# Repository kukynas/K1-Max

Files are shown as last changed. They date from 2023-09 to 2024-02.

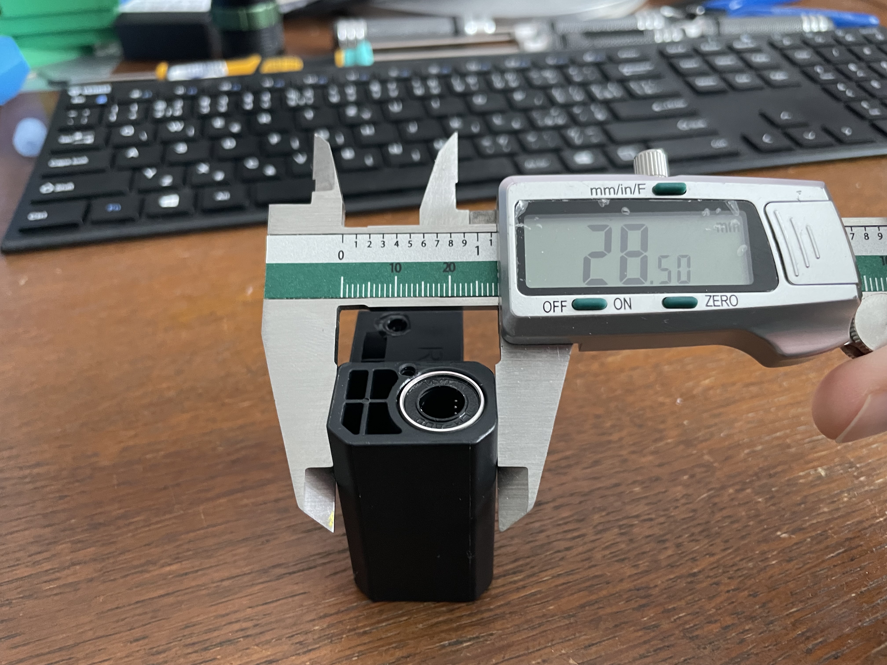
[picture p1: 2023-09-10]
Photo/IMG_5438.JPG

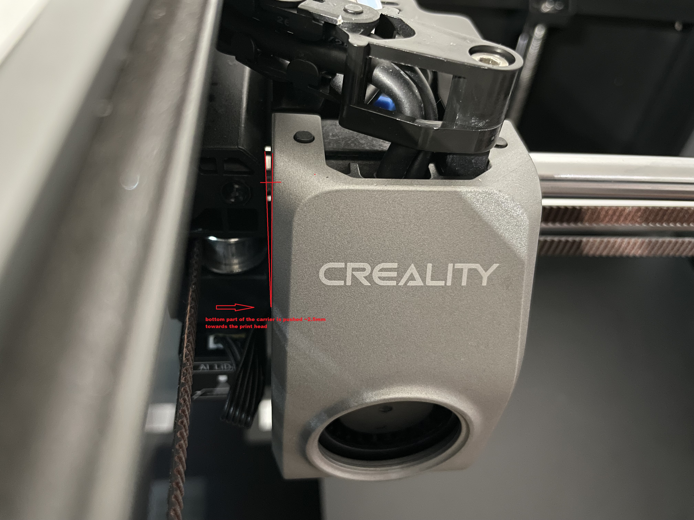
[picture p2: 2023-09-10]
Photo/IMG_5382s.jpg

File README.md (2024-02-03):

# K1 Max
Everything related to Creality K1 Max printer

Work in progress...

Attribution-NonCommercial-ShareAlike 4.0 International (CC BY-NC-SA 4.0)

## Acknowledgements

 - [D3vil Design](https://github.com/D3vil-Design)
 - [Henlor](https://www.printables.com/search/models?q=henlor&ctx=models)
 - And many others

### More info related to K1/Max mods...

Discord: https://discord.gg/QVAN5VNf

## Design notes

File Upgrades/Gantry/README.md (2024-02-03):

# About this mod
It mainly fixes dimensional accuracy, belt path and improve input shaper resonances for both XY axis, the XY rods have much better support by adding mass to the stepper/idler mounts and XY joints, this is full update with new XY joints, new stepper mounts and new idler mounts. One important fact, you'll lose about 5mm of your X travel but build area is bigger than the allowed print area so all should remain the same from print size perspective, you might need to update your printer.cfg if needed and shorten the X travel by few mm, make sure you watch your gantry for the first time as I couldn't test it on K1 (only K1 Max). Gantry is compatible with 16T-26T stepper pulleys so for stepper motors you either use your existing and just change the pulleys to 16T-26T or you'll need new steppers and new pulleys, maximum size of the pulleys allowed is 26T, you will also need to change your printer.cfg parameters, "rotation_distance:" for both X and Y steppers according to your chosen pulley (i.e. 20T x 2mm = 40), sensorless homing "driver_SGTHRS:" for both X and Y, you need to experiment as there's no rule for the correct number, start with 100, if the toolhead doesn't move then go down in 5 increments (95, 90, etc.) if the toolhead is smashing against the frame you need to increase the number (105,110, etc), you might need to cut few teeth from your original belts, how much depends on pulleys chosen, make sure you won't cut too much so that your tensioners are released as much as possible to keep suficient amount of belt/pulley teeth contact for sufficient grip 

# Print setting, orientation etc.
Print with ASA, ABS, PA6/12, PET or any other high temp material, 35-40% infill, 0.16mm layer hight, 4 walls, 8 top/bottom layers, with support as per sliced sample below 




Tolerances are really tigth to prevent potential wobble over time but trimming is not necessary, push/pull the rods in/out couple of times   

# BOM
XY joints:

- 8 x F623ZZ (3x10x4mm) flanged bearings
- 4 x M3x20mm grub screw
- 4 x 0.1-0.2mm M3 washer (between bearings = bearing->washer->bearing)
- 2 x original LM8LUU bearings
- 2 x original M3 screws holding bearings in place

.

Stepper Mounts:

- 12 x F624-2RS or ZZ (4x13x5mm) flanged bearings
- 6 x 0.1-0.2mm M4 washer (between bearings = bearing->washer->bearing)
- 8 x 3x5x5 heat insert
- 8 x M3x6 FHCS screw
- 4 x 0.5mm M3 washer (under the tensioner release screws)
- all the other original parts (tensioners, tensioner idler pin, tensioning screws, stepper screws, original washer used between idlers)

.

Idler Mounts:

- 4 x F624-2RS or ZZ (4x13x5mm) flanged bearings
- 2 x M4x20mm grub screw
- 2 x 0.1-0.2mm M4 washer (between bearings = bearing->washer->bearing)
- 8 x 3x5x5 heat insert
- 8 x M3x6 FHCS screw






.

### More info related to K1/Max mods...

https://discord.gg/QVAN5VNf

Attribution-NonCommercial-ShareAlike 4.0 International (CC BY-NC-SA 4.0)

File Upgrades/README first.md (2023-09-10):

# Print setting for XY joints
Print with ASA, PA6/12, PET or any other higher temp material

Layer height 0.12mm

30% infill

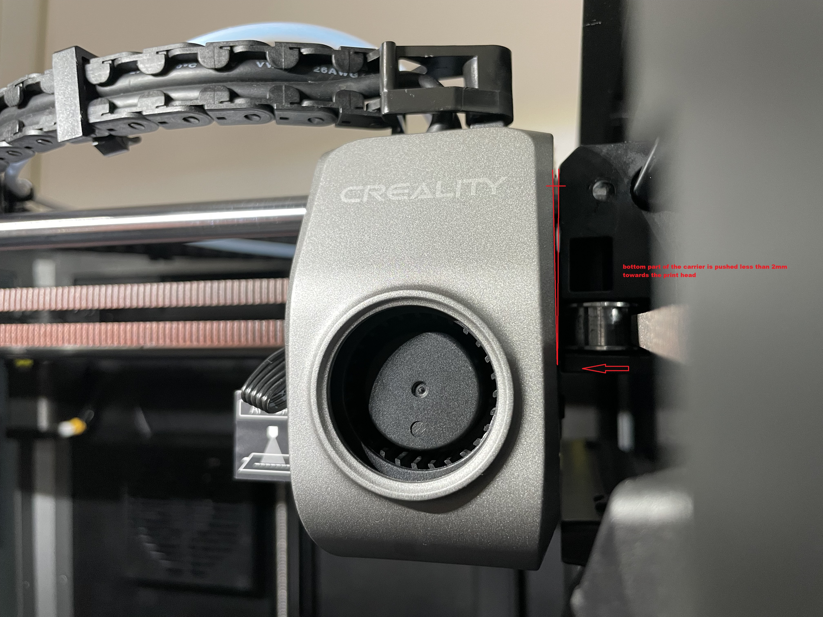
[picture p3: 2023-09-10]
Photo/IMG_5379s.jpg

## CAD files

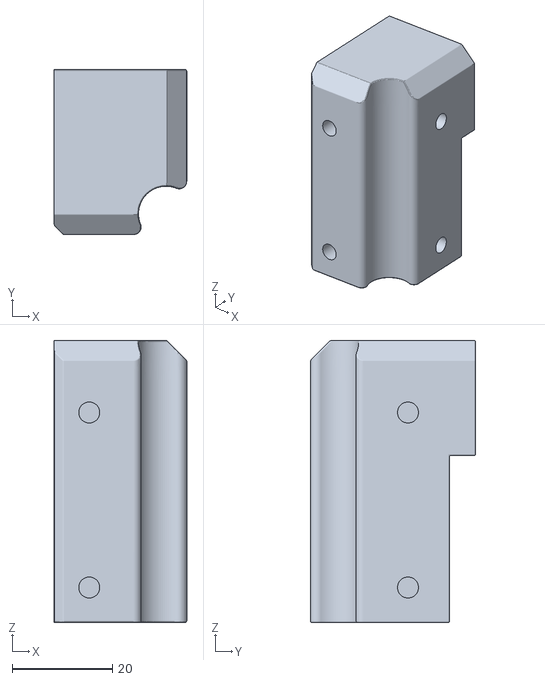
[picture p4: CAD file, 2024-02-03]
Upgrades/Gantry/K1 Idler mount right v17.stl
26.5 x 33.0 x 56.4

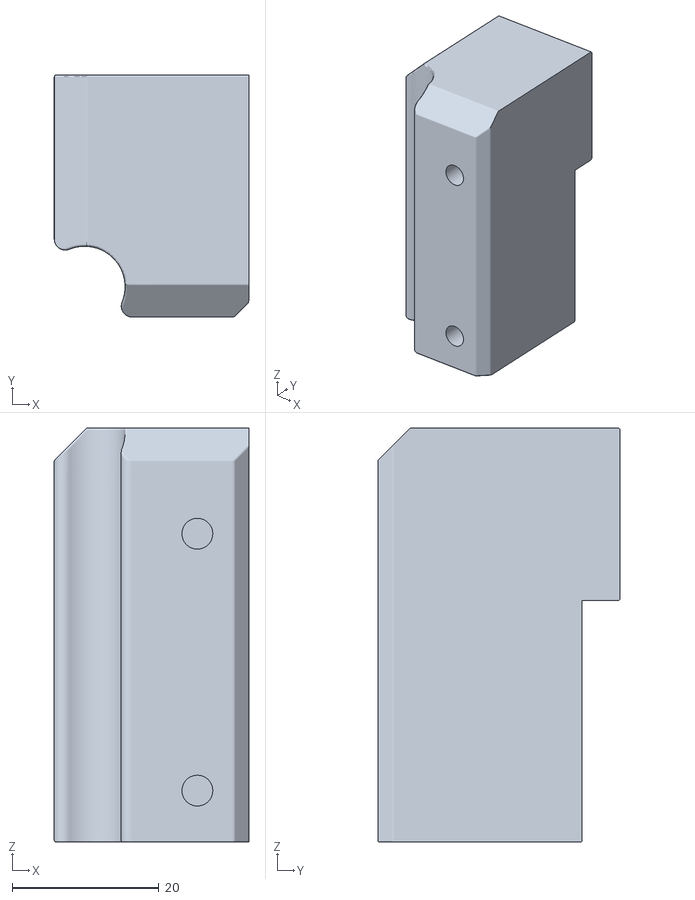
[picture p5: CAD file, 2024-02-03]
Upgrades/Gantry/K1 Idler mount left v17.stl
26.5 x 33.0 x 56.4

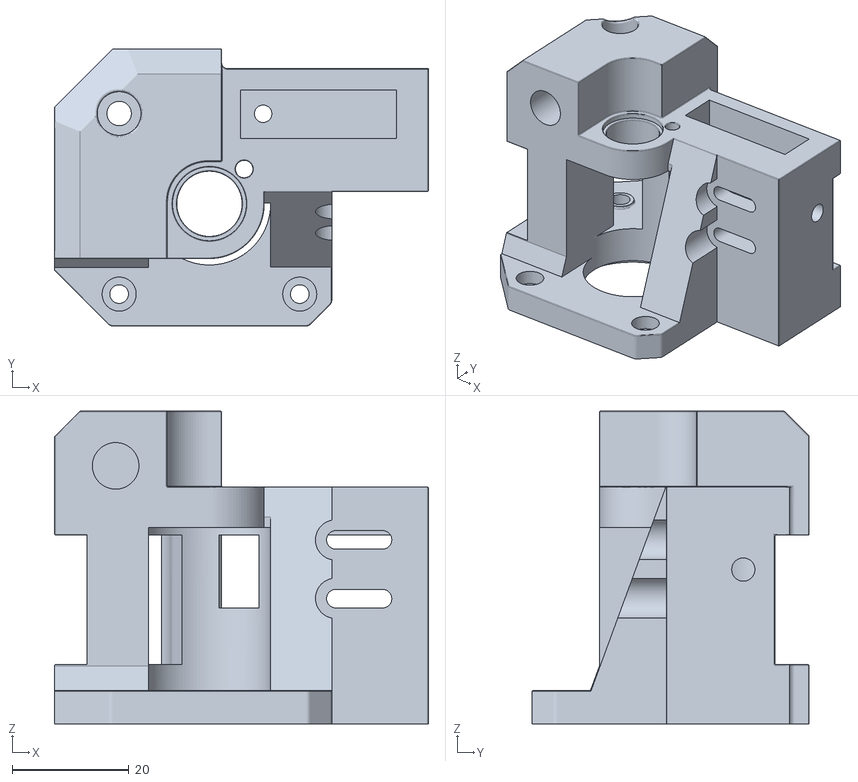
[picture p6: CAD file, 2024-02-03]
Upgrades/Gantry/K1 Stepper Mount left V17.stl
64.2 x 47.6 x 53.7

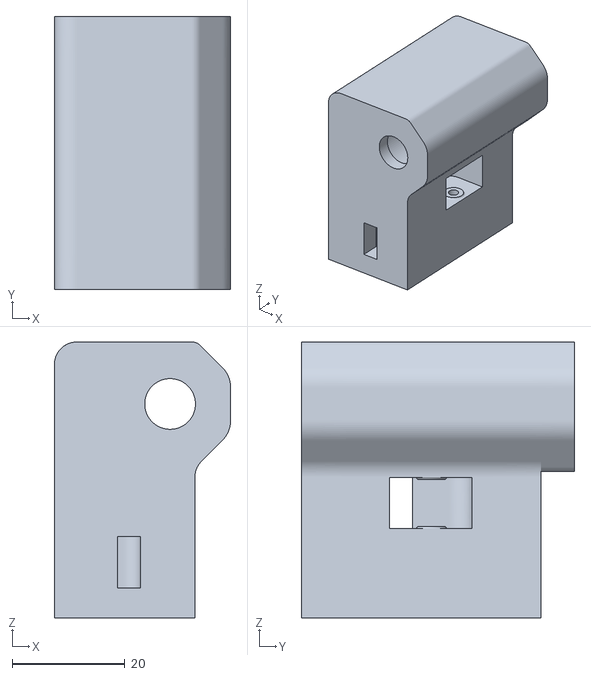
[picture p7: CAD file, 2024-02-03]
Upgrades/Gantry/K1 XY joint right v17.stl
31.3 x 48.5 x 49.0

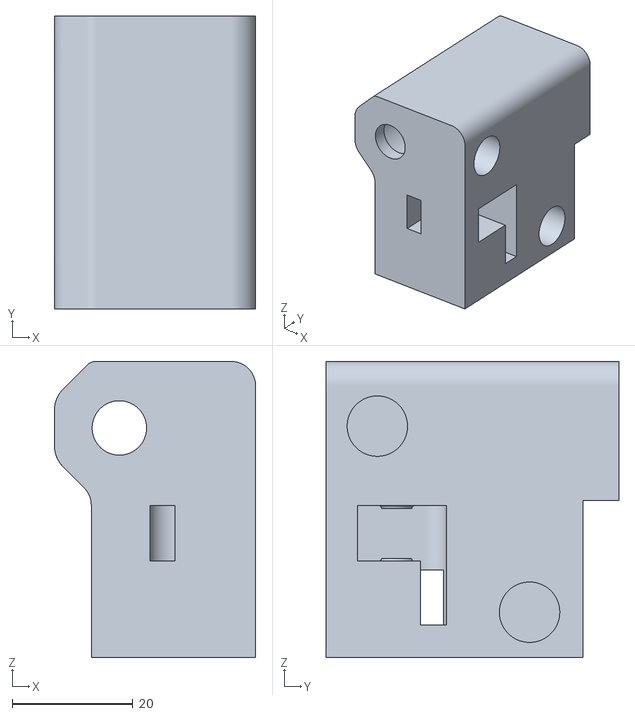
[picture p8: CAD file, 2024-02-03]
Upgrades/Gantry/K1 XY joint left V17.stl
33.3 x 48.5 x 49.0

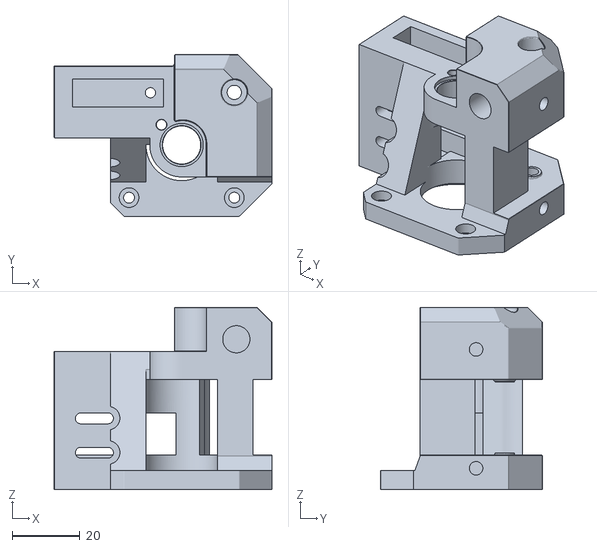
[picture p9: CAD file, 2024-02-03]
Upgrades/Gantry/K1 Stepper Mount right V17.stl
64.2 x 47.6 x 53.7

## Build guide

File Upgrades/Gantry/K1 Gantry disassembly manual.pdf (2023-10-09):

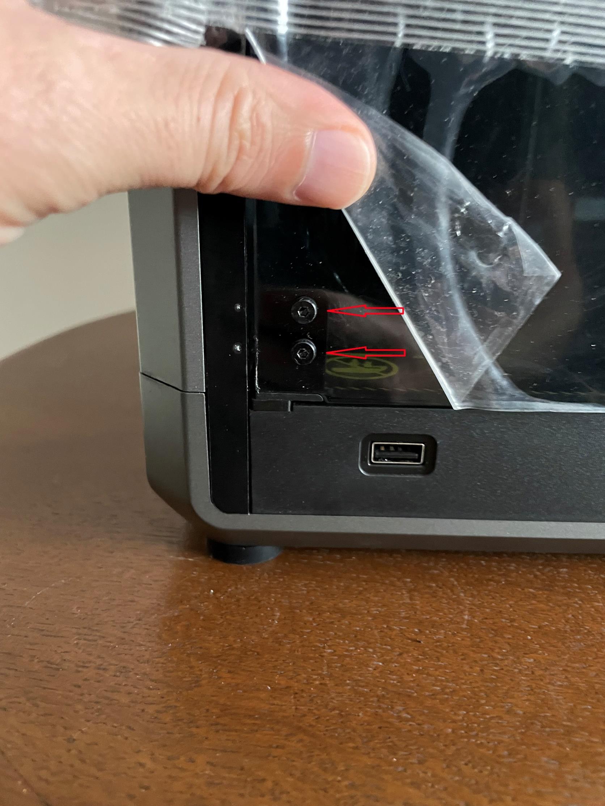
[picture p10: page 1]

First of all remove the front door and acrylic side panels

Release the screw on bottom hinge, next release the screws on top hinge as per below pictures, be carefull and hold the doors with your hand

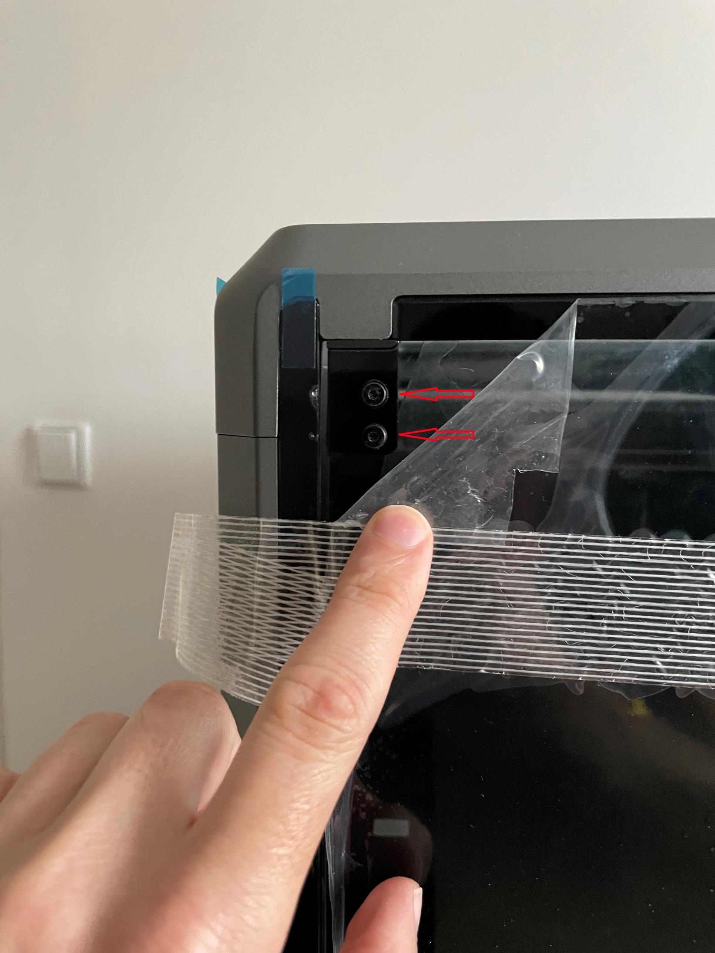
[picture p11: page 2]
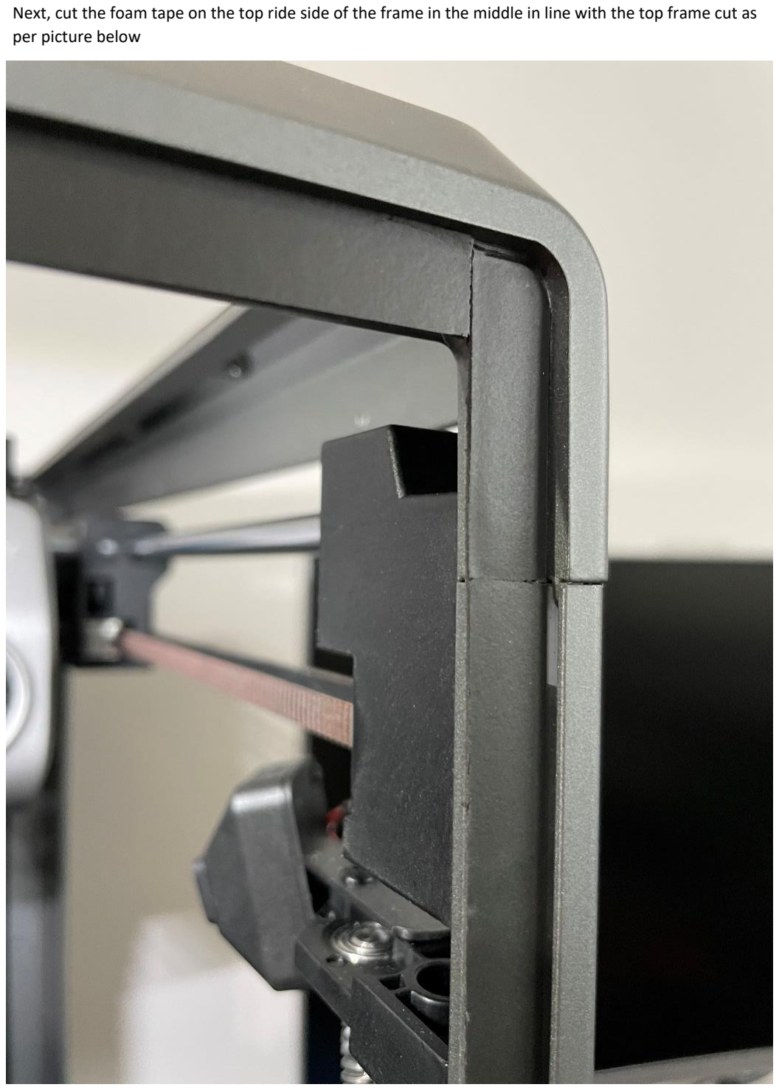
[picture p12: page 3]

Next, cut the foam tape on the top ride side of the frame in the middle in line with the top frame cut as per picture below

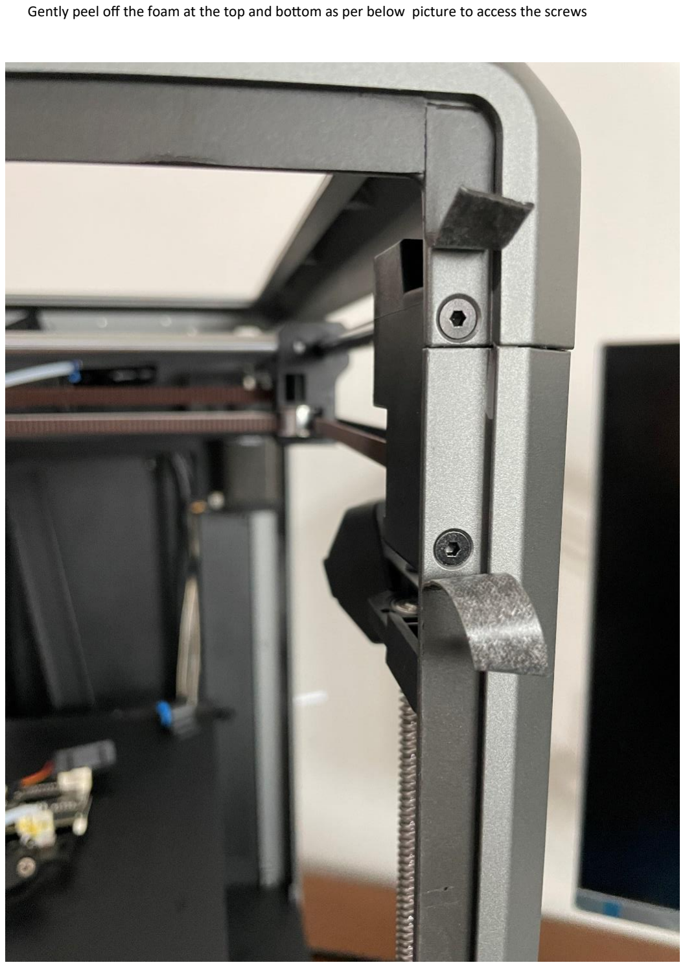
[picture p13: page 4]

Gently peel off the foam at the top and bottom as per below picture to access the screws

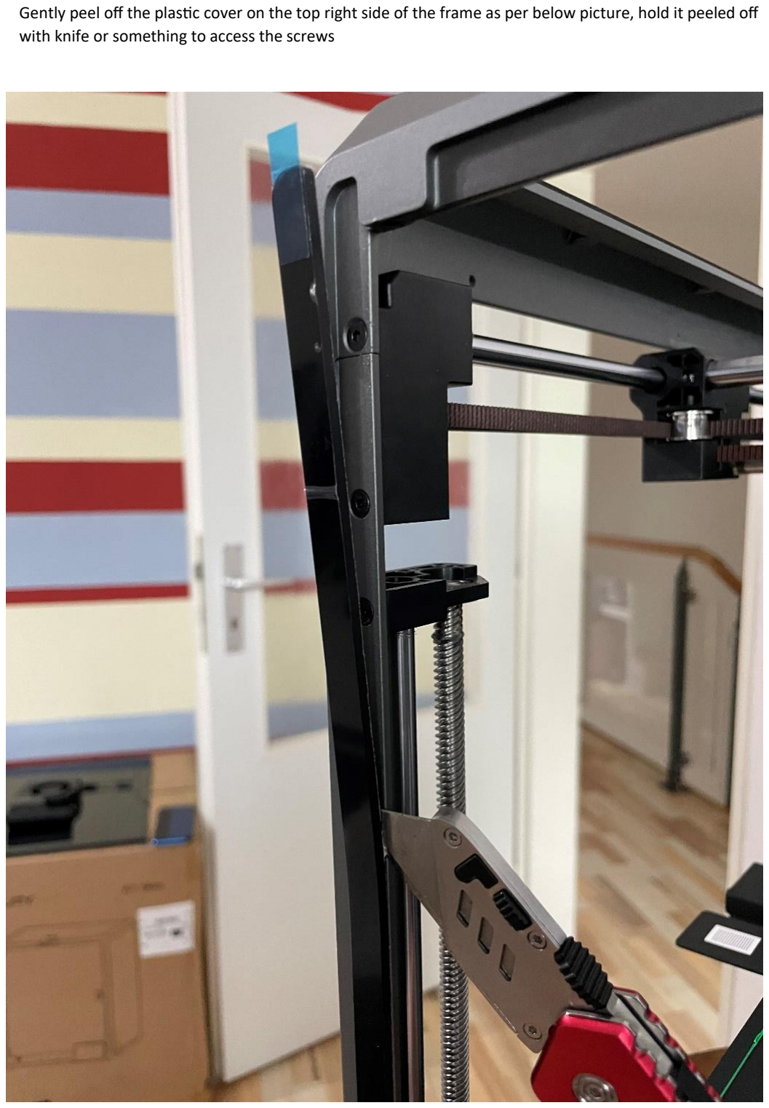
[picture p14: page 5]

Gently peel off the plastic cover on the top right side of the frame as per below picture, hold it peeled off with knife or something to access the screws

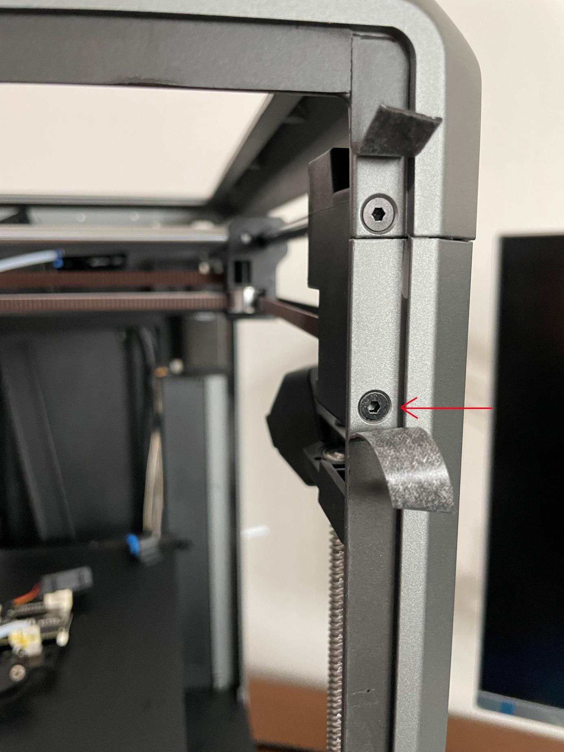
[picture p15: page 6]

Unscrew all the bolts as indicated by red arrow on below pictures, front right top

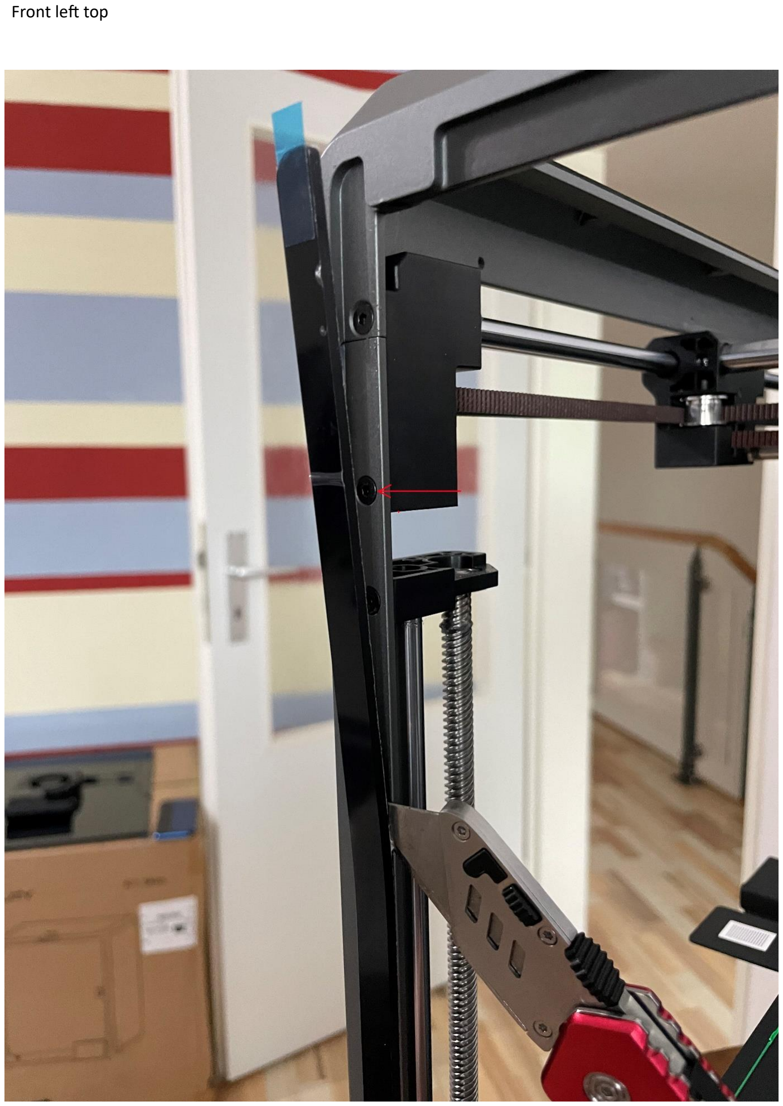
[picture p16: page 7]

Front left top

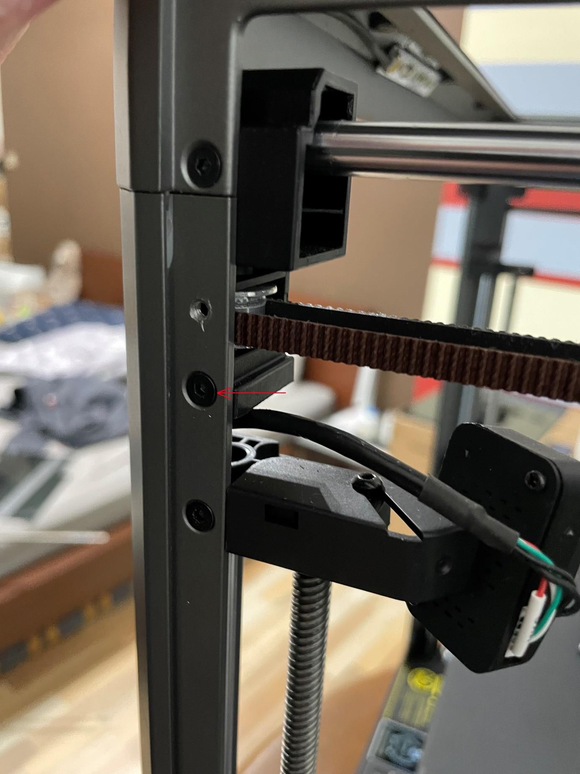
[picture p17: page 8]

Right side top front

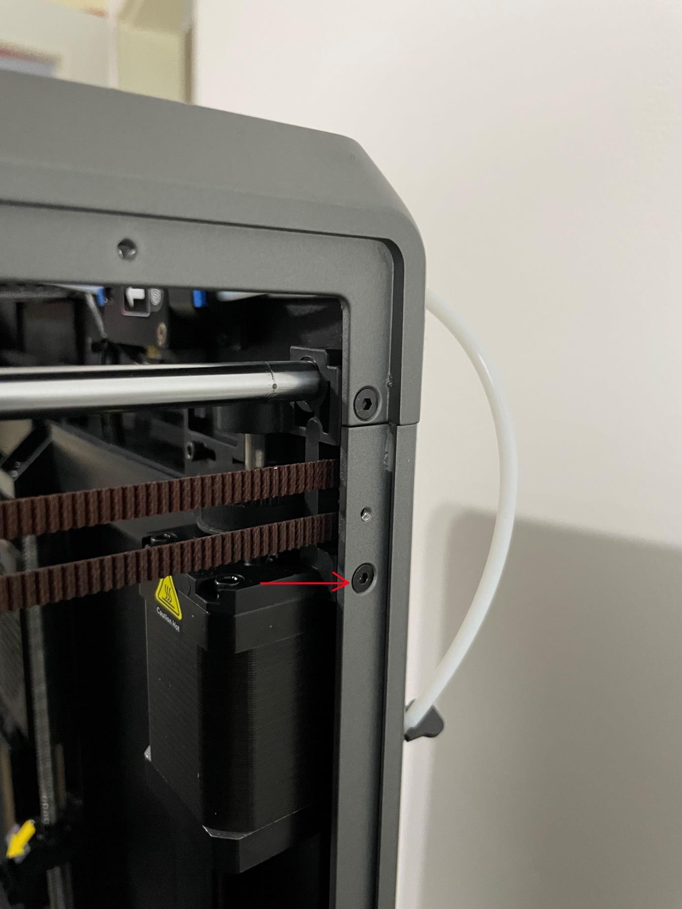
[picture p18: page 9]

Right side top back

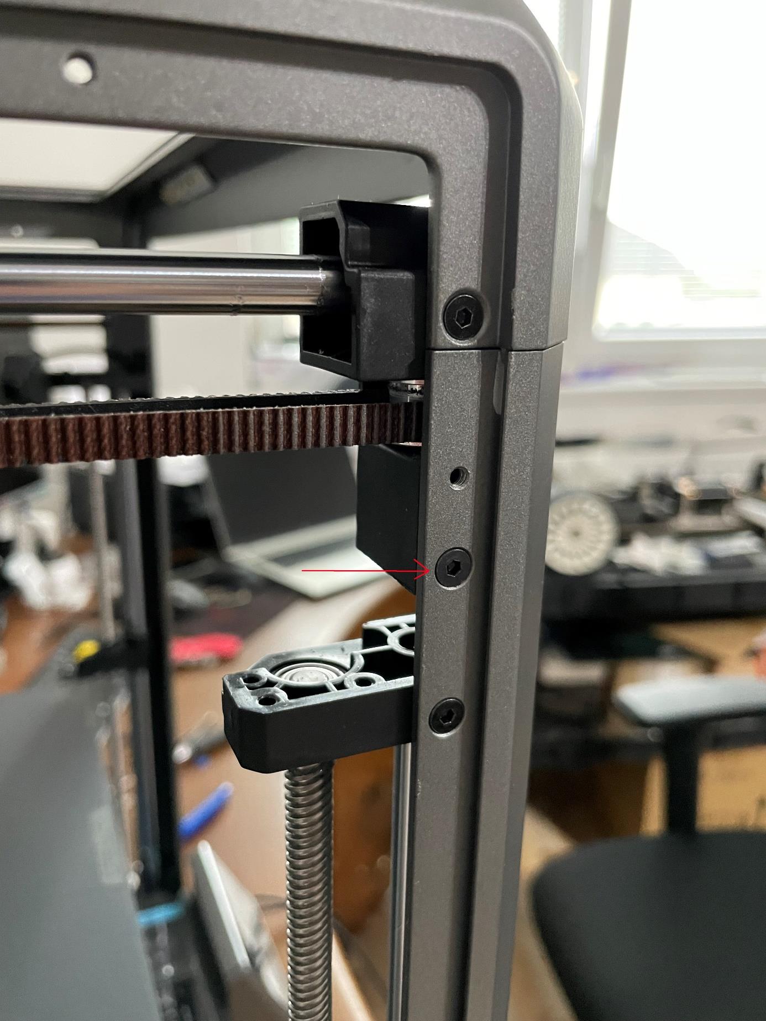
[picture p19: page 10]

Left side Top front

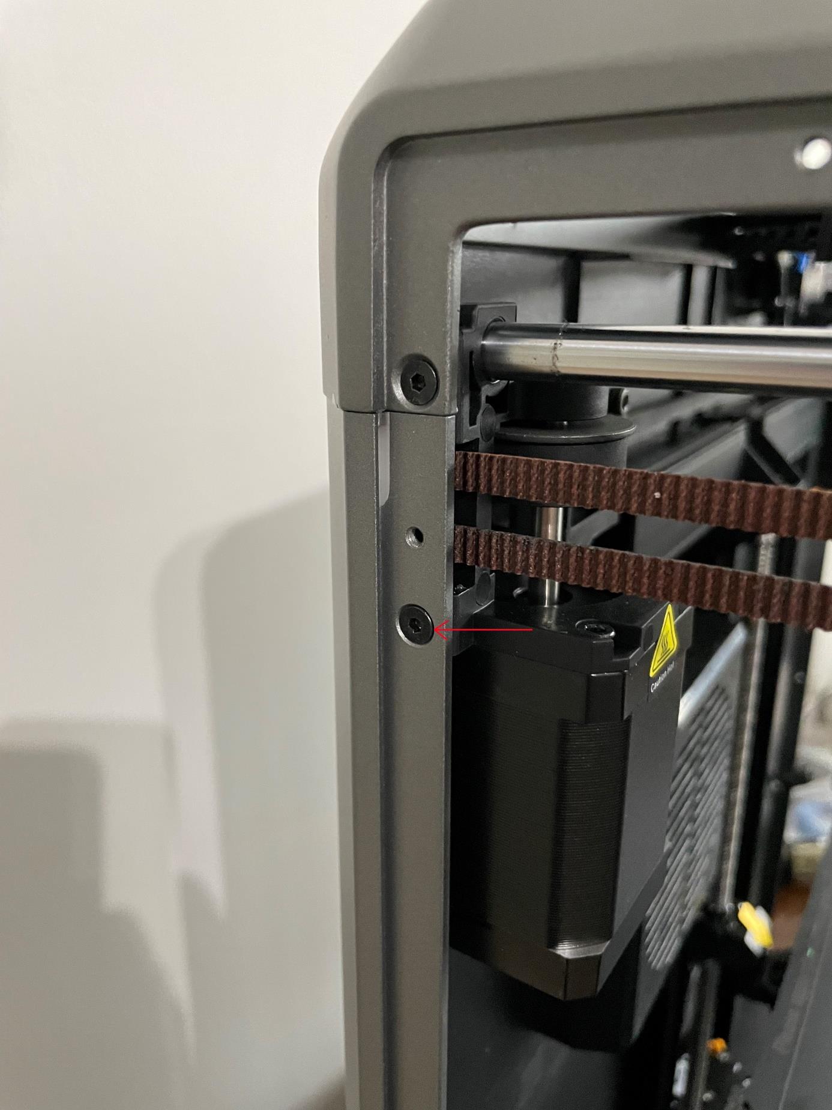
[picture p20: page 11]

Left side top back

Back panel

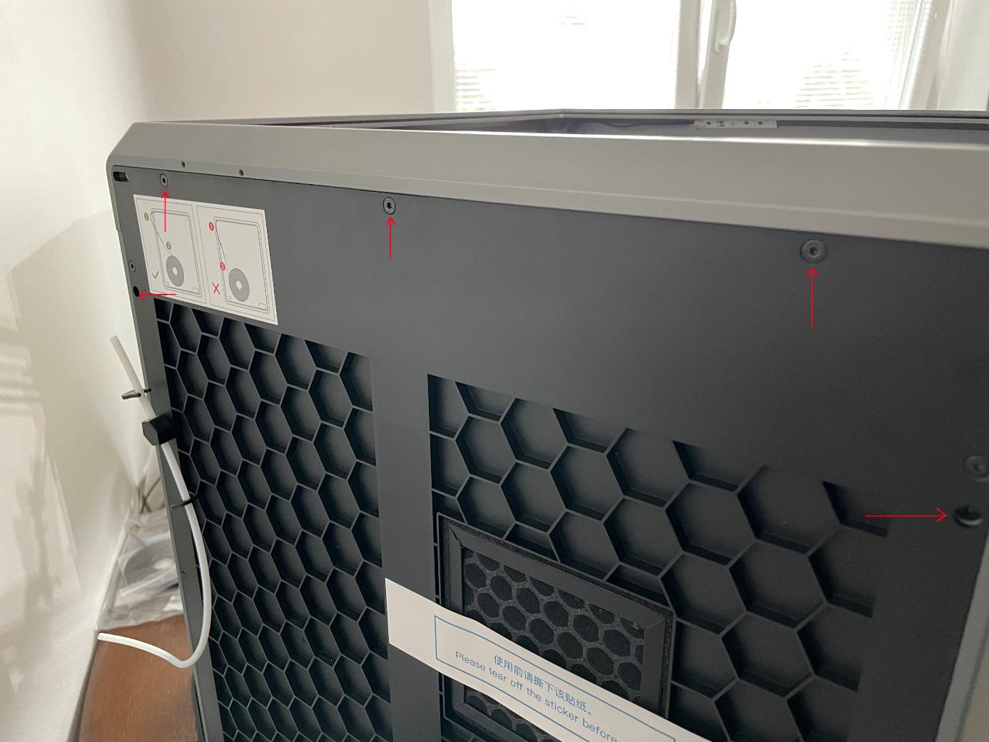
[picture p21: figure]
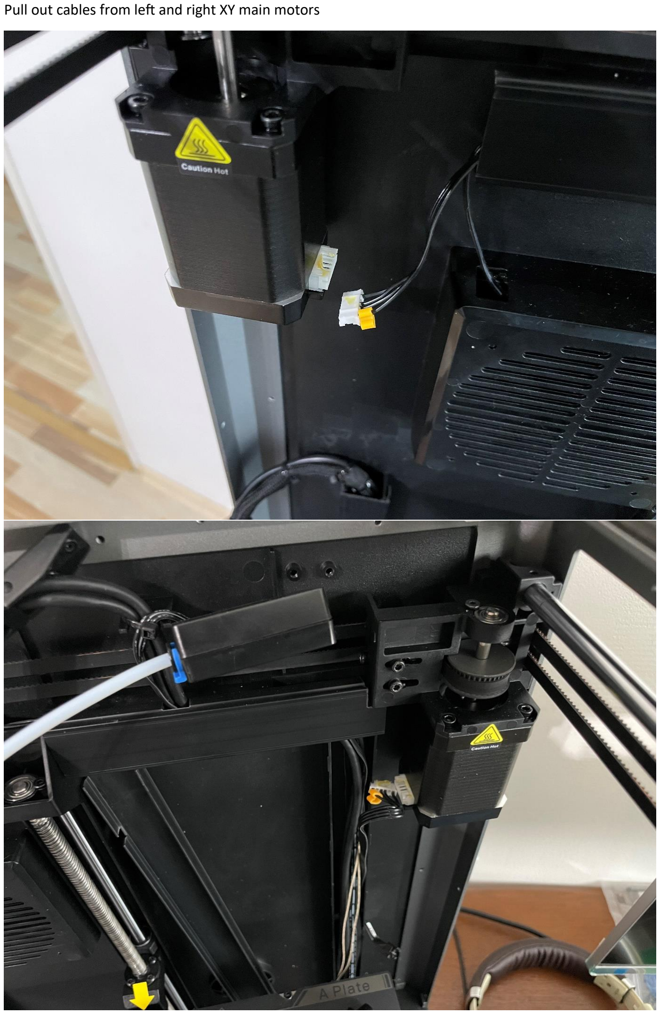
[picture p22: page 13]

Pull out cables from left and right XY main motors

Unscrew the drag chain, filament runout sensor and PTFE holder from the top frame

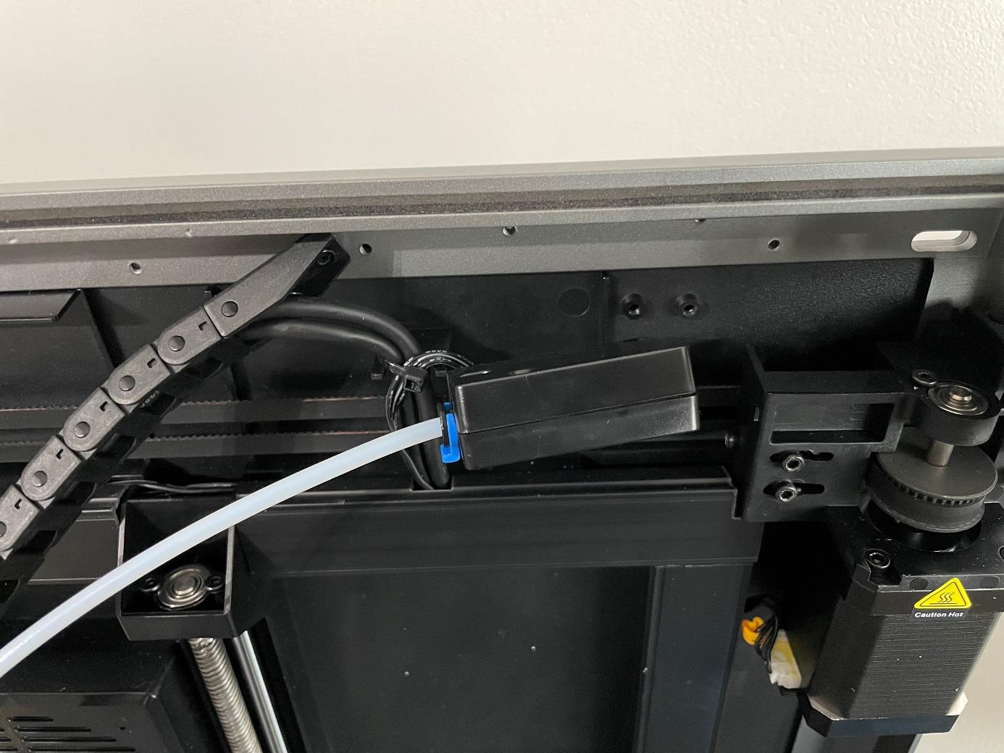
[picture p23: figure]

Disconnect the drag chain from the print head, this will require to disassemble the print head, mainly the main board, lidar sensor, front cover with fan and disconnecting the hotend heater and thermistor from the main board and finally extruder motor, also pull out the ptfe tube so that the print head is no more attached to the drag chain

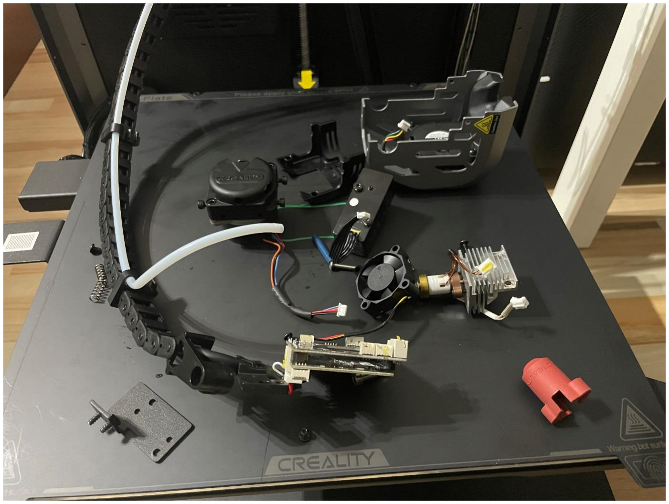
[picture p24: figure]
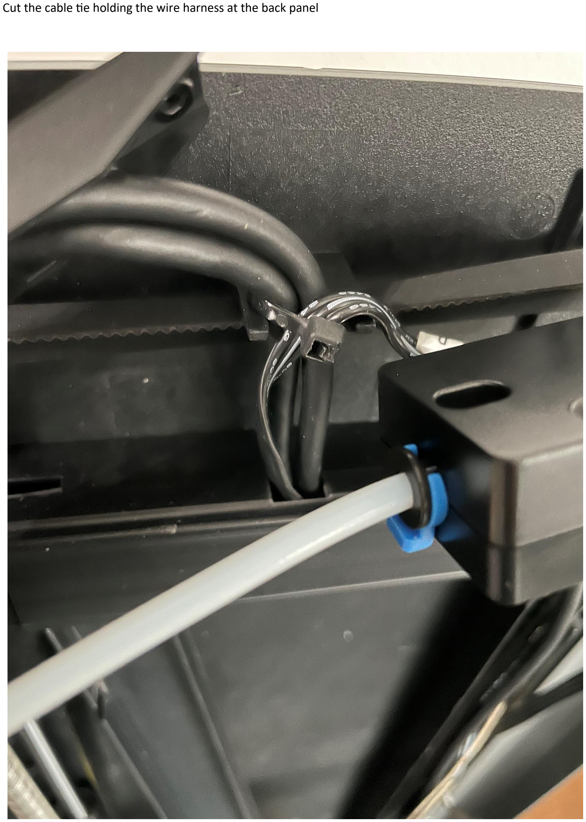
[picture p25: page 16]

Cut the cable tie holding the wire harness at the back panel

Disconnect LED strip from the front top inside of the frame…

I may have forgotten something so be gentle but now you should be able to pull out the top frame with entire XY motion system

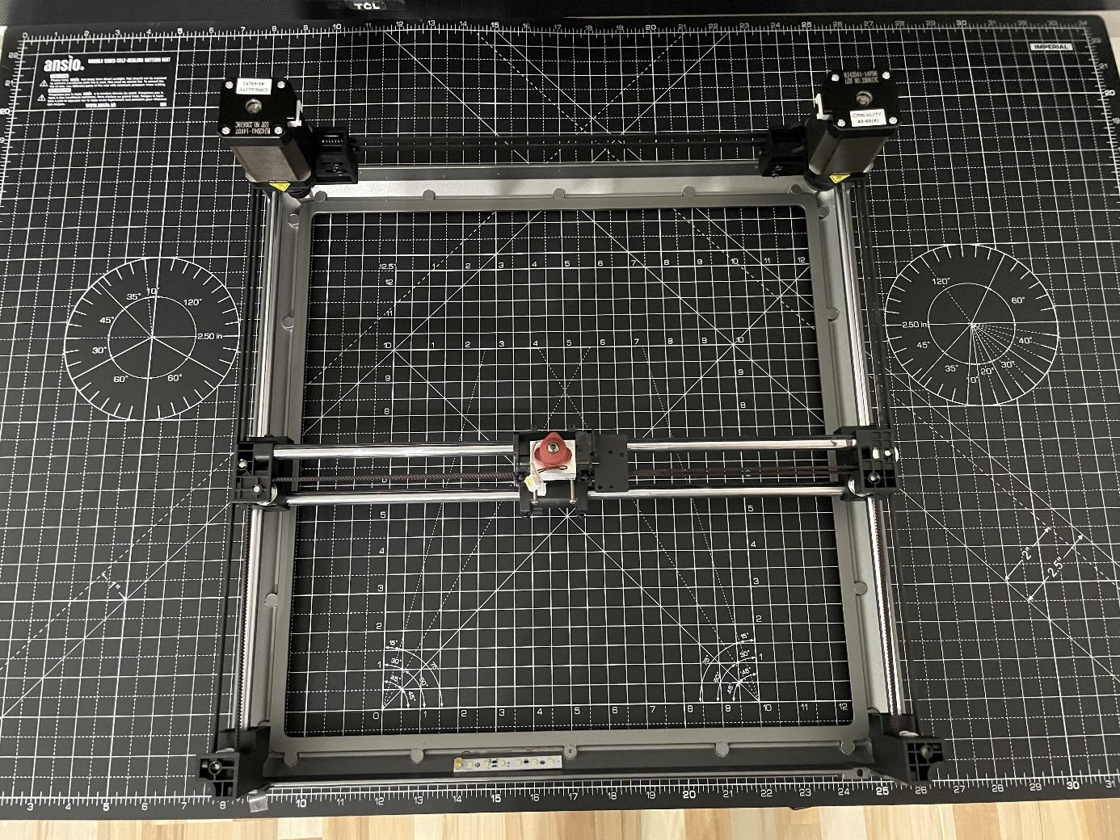
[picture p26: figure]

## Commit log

2023-09-10 Update and rename XY JOINT V3DD v7.step to XY JOINT V3DD v7 extra size.step
    [XY JOINT V3DD v7 extra size.step]
2024-02-03 Create Gantry
